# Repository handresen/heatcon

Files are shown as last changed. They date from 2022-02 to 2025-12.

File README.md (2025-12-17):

# HeatCon
Simple controller for water based floor heating.
The project was initiated when the old controller for the floor heating in our house broke down. I wanted the ability to control floor heating remotely from mobile and web. A prototype has been up and running for six weeks now without any problems.

## Summary
* Solid state switches (mosfets)
* Optocouplers to isolate MCU from 24V
* ESP8266 socket (WeMos D1 mini)
* Integrated switching power 24V-3.3V, single power for MCU and actuators
* No moving parts (ie no magnetic relays)
* EPS8266 powers opto couplers, mosfets drive the actuators
* Optionally separate ground and power for MCU and actuators
* Should work well for other actuators 6V-30V, up to 2.5A/channel (limited by PCB trace widths, more with thicker Cu)

## Schema


## Layout
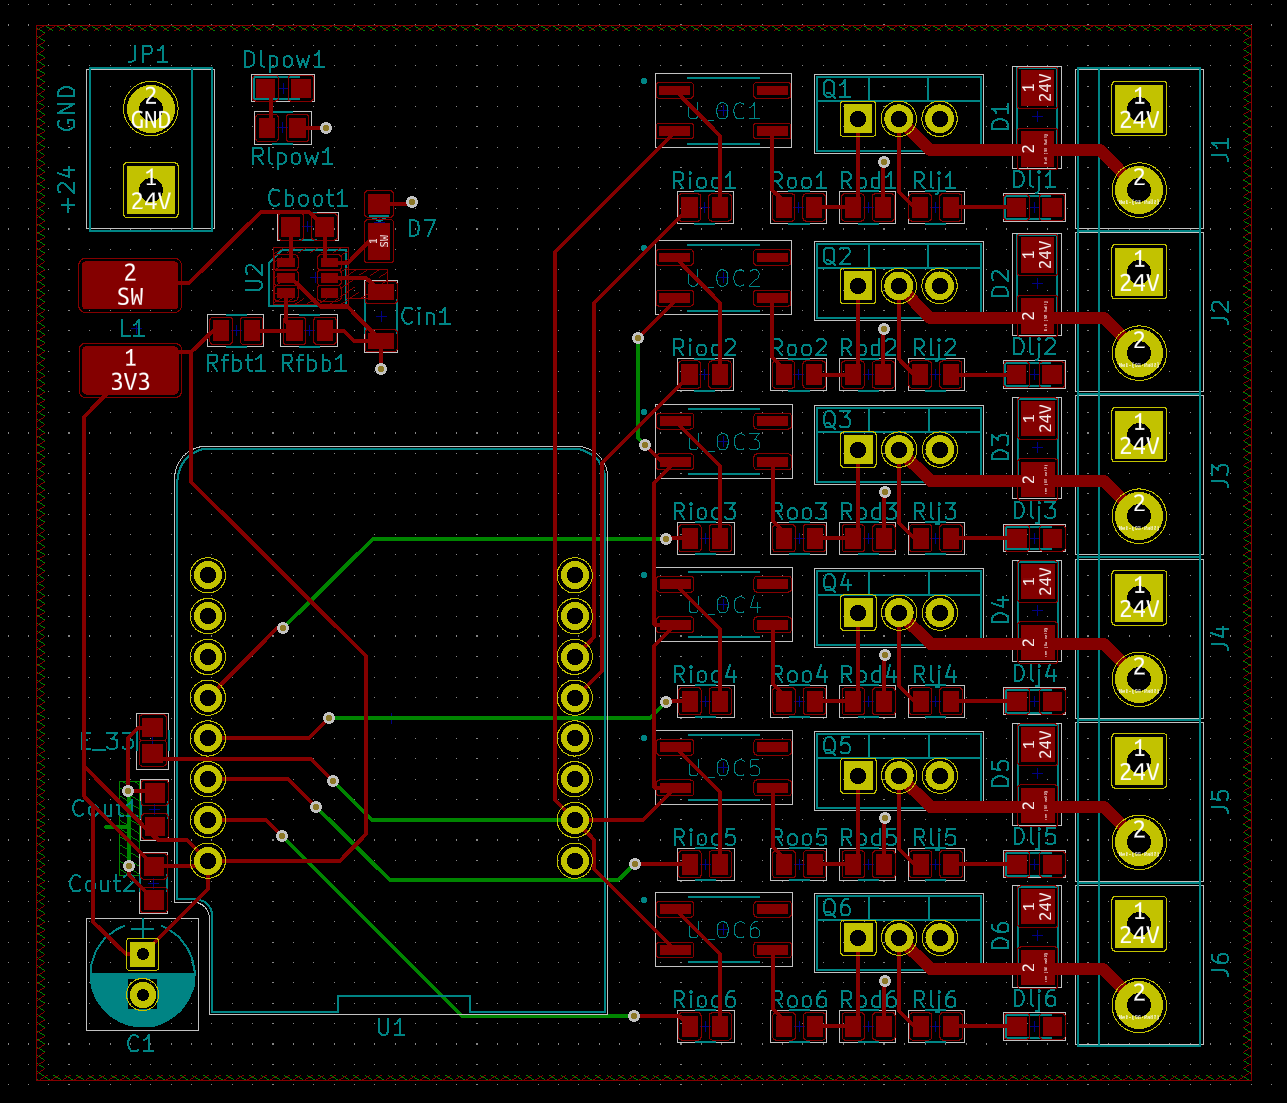
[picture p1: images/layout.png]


## Model
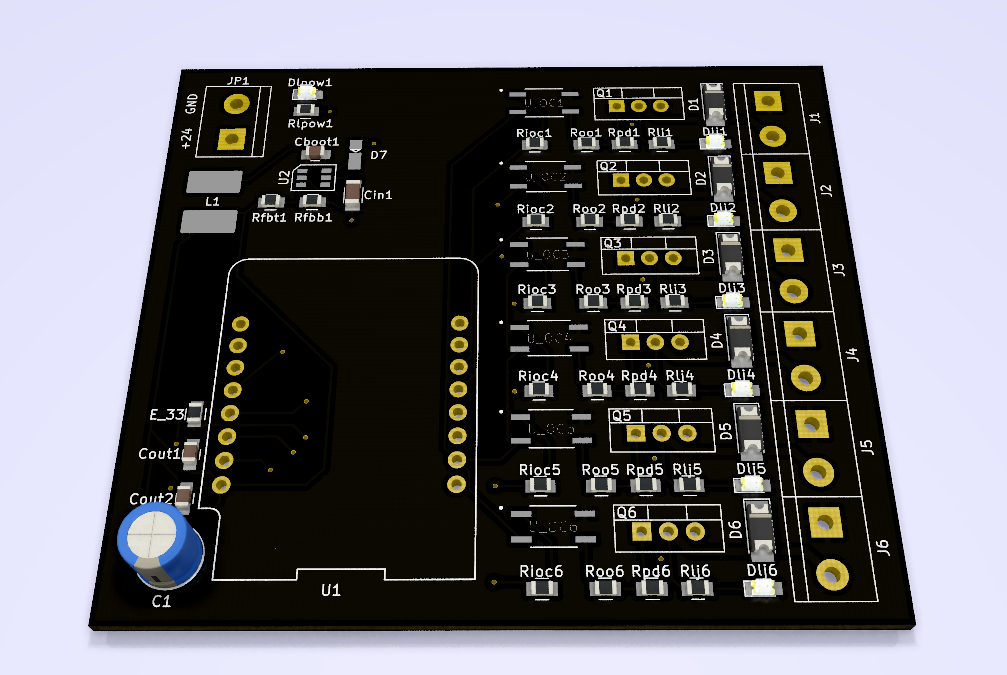
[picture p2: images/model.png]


## PCB
PCB by https://jlcpcb.com/, ENIG with black solder mask
<br/><br/>
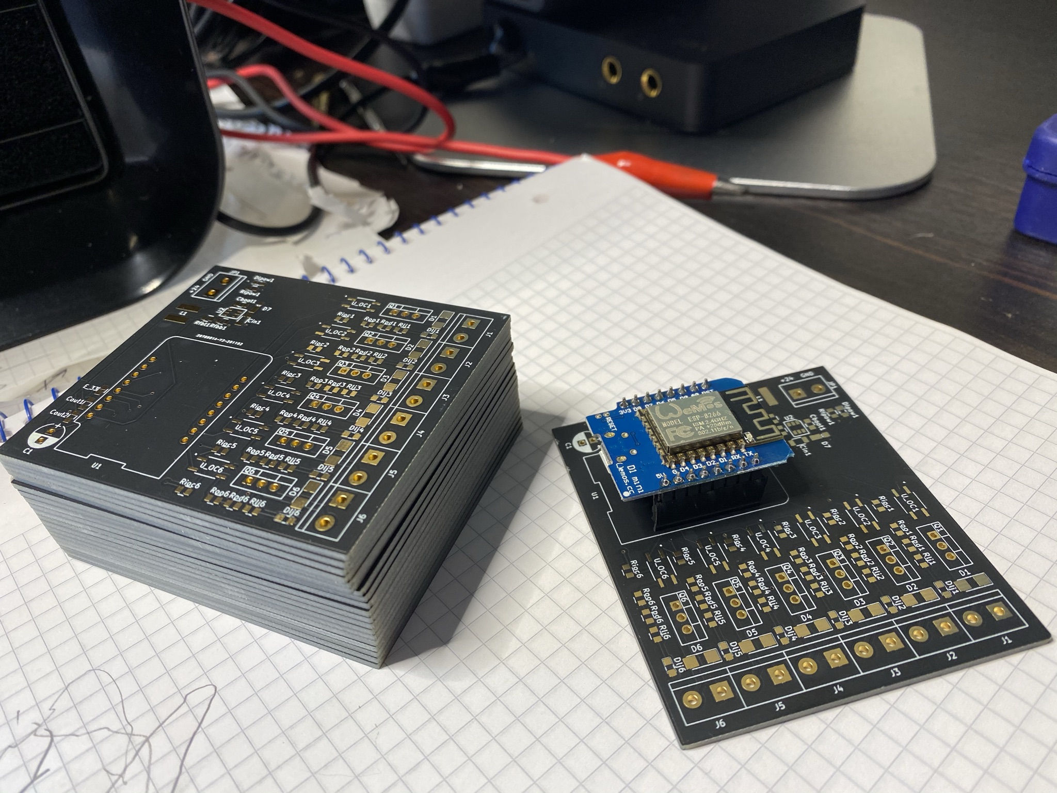
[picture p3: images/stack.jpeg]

<br/>
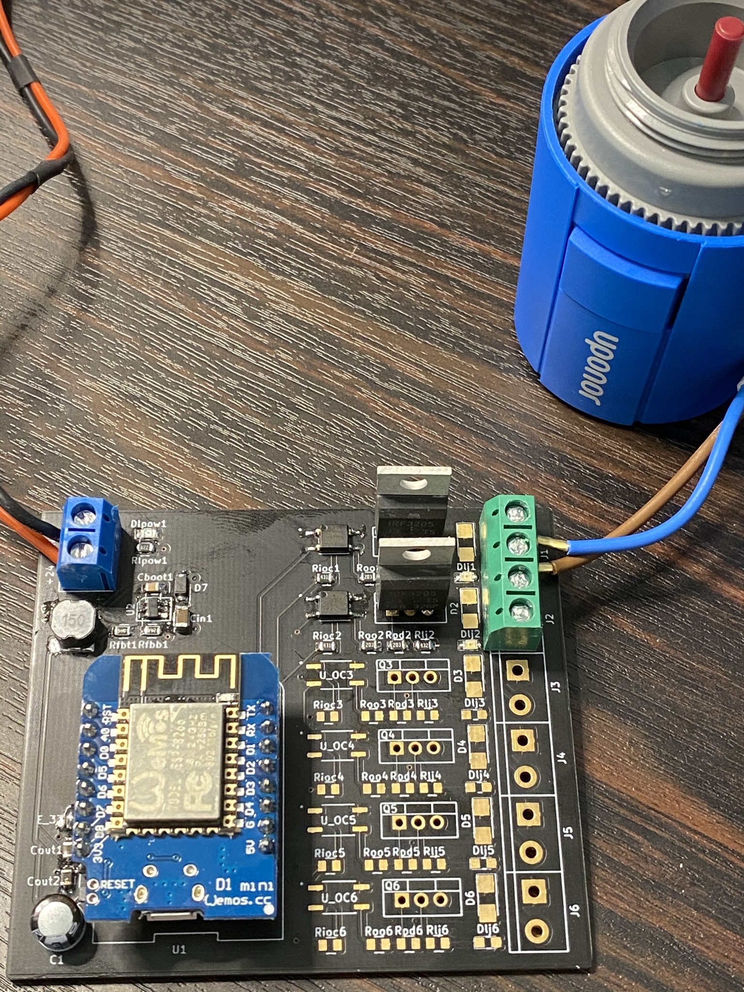
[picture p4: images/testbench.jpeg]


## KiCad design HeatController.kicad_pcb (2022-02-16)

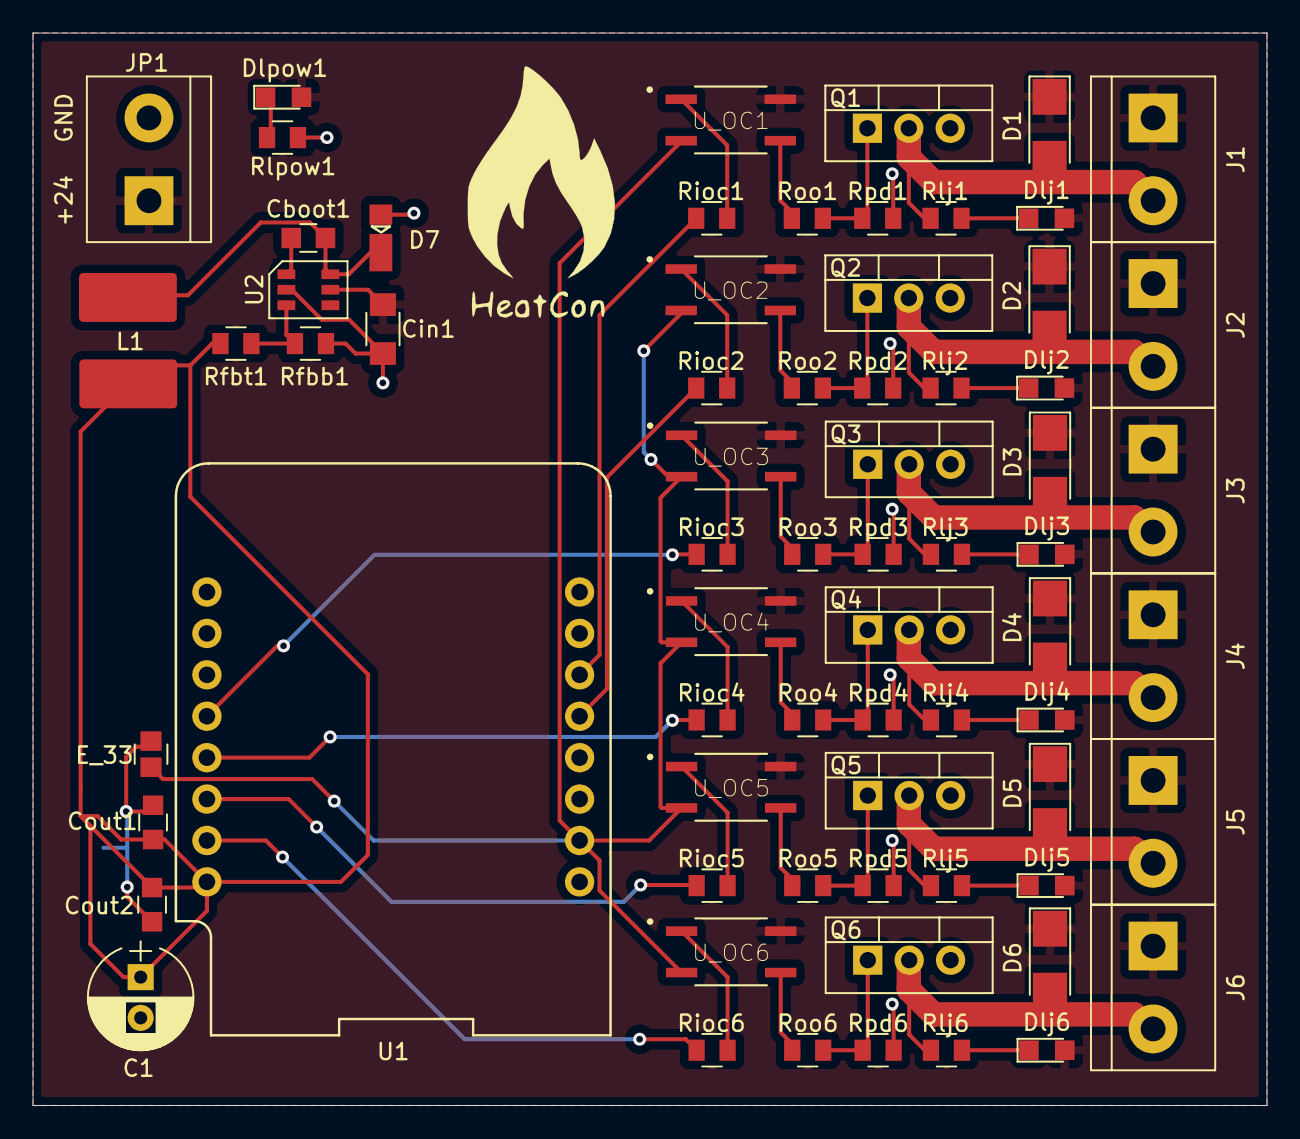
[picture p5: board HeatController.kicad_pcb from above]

Board: 2 copper layers, 75.7 x 65.8 mm, 69 parts (0 on the bottom side), 44 nets.

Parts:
C1: 100uF; CP_Radial_D6.3mm_P2.50mm
Cboot1: 100nF; C_0805_H
Cin1: 4.7uF; C_1206
Cout1, Cout2: 22uF; C_0805_H
D1, D2, D3, D4, D5, D6: 1N4007; DO-214AC
D7: 600mV; SOD-123EP
Dlj1, Dlj2, Dlj3, Dlj4, Dlj5, Dlj6: LED; LED_0805
Dlpow1: LED; LED_0805
E_33: 0; R_0805_SHORT
J1, J2, J3, J4, J5, J6: Screw_Terminal_01x02; TerminalBlock_bornier-2_P5.08mm_tight
JP1: Screw_Terminal_01x02; TerminalBlock_bornier-2_P5.08mm_tight
L1: 15uH; SRN_INDUCTOR
Q1, Q2, Q3, Q4, Q5, Q6: IRF3205; TO-220-3_Vertical
Rfbb1: R; R_0805_H
Rfbt1: 64.9k; R_0805_H
Rioc1, Rioc2, Rioc3, Rioc4, Rioc5, Rioc6: 400; R_0805_H
Rlj1, Rlj2, Rlj3, Rlj4, Rlj5, Rlj6: 7k; R_0805_H
Rlpow1: 7k; R_0805_H
Roo1, Roo2, Roo3, Roo4, Roo5, Roo6: 20k; R_0805_H
Rpd1, Rpd2, Rpd3, Rpd4, Rpd5, Rpd6: 20k; R_0805_H
U1: WeMos_D1_mini; wemos-d1-mini-with-pin-header
U2: LMR14010ADDC; LRM14010A
U_OC1, U_OC2, U_OC3, U_OC4, U_OC5, U_OC6: EL357N(A)(TA)-G; SOP254P700X200-4N

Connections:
/3V3: C1.1, Cout1.1, Cout2.1, L1.1, Rfbt1.1, U1.8
/24V: Cin1.1, D1.1, D2.1, D3.1, D4.1, D5.1, D6.1, Dlj1.2, Dlj2.2, Dlj3.2, Dlj4.2, Dlj5.2, Dlj6.2, Dlpow1.2, J1.1, J2.1, J3.1, J4.1, J5.1, J6.1, JP1.1, U2.5, U_OC1.4, U_OC2.4, U_OC3.4, U_OC4.4, U_OC5.4, U_OC6.4
/D1: Rioc1.2, U1.14
/D2: Rioc2.2, U1.13
/D5: Rioc3.2, U1.4
/D6: Rioc4.2, U1.5
/D7: Rioc5.2, U1.6
/D8: Rioc6.2, U1.7
/GND2: E_33.1, U1.10, U_OC1.2, U_OC2.2, U_OC3.2, U_OC4.2, U_OC5.2, U_OC6.2
/SW: Cboot1.2, D7.1, L1.2, U2.6
GND: C1.2, Cin1.2, Cout1.2, Cout2.2, D7.2, E_33.2, JP1.2, Q1.3, Q2.3, Q3.3, Q4.3, Q5.3, Q6.3, Rfbb1.2, Rlpow1.1, Rpd1.2, Rpd2.2, Rpd3.2, Rpd4.2, Rpd5.2, Rpd6.2, U2.2
unnamed: Cboot1.1, U2.1
unnamed: D1.2, J1.2, Q1.2, Rlj1.2
unnamed: D2.2, J2.2, Q2.2, Rlj2.2
unnamed: D3.2, J3.2, Q3.2, Rlj3.2
unnamed: D4.2, J4.2, Q4.2, Rlj4.2
unnamed: D5.2, J5.2, Q5.2, Rlj5.2
unnamed: D6.2, J6.2, Q6.2, Rlj6.2
unnamed: Dlj1.1, Rlj1.1
unnamed: Dlj2.1, Rlj2.1
unnamed: Dlj3.1, Rlj3.1
unnamed: Dlj4.1, Rlj4.1
unnamed: Dlj5.1, Rlj5.1
unnamed: Dlj6.1, Rlj6.1
unnamed: Dlpow1.1, Rlpow1.2
unnamed: Q1.1, Roo1.2, Rpd1.1
unnamed: Q2.1, Roo2.2, Rpd2.1
unnamed: Q3.1, Roo3.2, Rpd3.1
unnamed: Q4.1, Roo4.2, Rpd4.1
unnamed: Q5.1, Roo5.2, Rpd5.1
unnamed: Q6.1, Roo6.2, Rpd6.1
unnamed: Rfbb1.1, Rfbt1.2, U2.3
unnamed: Rioc1.1, U_OC1.1
unnamed: Rioc2.1, U_OC2.1
unnamed: Rioc3.1, U_OC3.1
unnamed: Rioc4.1, U_OC4.1
unnamed: Rioc5.1, U_OC5.1
unnamed: Rioc6.1, U_OC6.1
unnamed: Roo1.1, U_OC1.3
unnamed: Roo2.1, U_OC2.3
unnamed: Roo3.1, U_OC3.3
unnamed: Roo4.1, U_OC4.3
unnamed: Roo5.1, U_OC5.3
unnamed: Roo6.1, U_OC6.3

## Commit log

2020-11-25 Initial commit w/files
    [HeatController.kicad_pcb, HeatController.sch]
2020-12-01 Added logo, thicker traces to terminals, gerbers
    [HeatController-B_Cu.gbr, HeatController-B_Mask.gbr, HeatController-Edge_Cuts.gbr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]
2022-02-16 backup lenovo
    [HeatController.kicad_pcb]
